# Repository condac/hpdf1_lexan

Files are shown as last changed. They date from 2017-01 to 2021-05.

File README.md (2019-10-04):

# HPD F1 Lexan version
Custom version of the HPD F1 to use lexan body. 

## About
This is my custom version of the HPD F1 by Kent Asplund. Ask questions and join discussion about these printed cars on Google+ https://plus.google.com/communities/117625327650679845498 You can also open an issue here on github if you have questions about the cars design or build process. 

## Material

All parts are designed to be printed in 100% infill. Use 2mm Perimiters and 0.15-0.2mm layer height as a start. Total material used is about 260g.

You can print every part in PLA and it will work suprisingly well. If you are printing this for the first time I recommend you print it in PLA or what ever your printer can handle best at first, and when something break you can print it in nylon.   

My race car have everything in PLA apart from some nylon changes I have made after some parts broke. There are 2 categories of nylon you want to use, a soft and flexible, and a hard. Where hard is still very soft compared to PLA. I have used Bridge nylon for flexible and 910 Alloy for harder. Here are my current changes and why:

* front_wing.stl & rear_wing.stl softer nylon for flex and impact resistance. (No rear wing in bridge nylon have been destroyed yet!!) 
* side_stab2.stl Soft or hard nylon for maximum impact resistance. I used Bridge here because it was in the printer at the time. 
* cradle_bottomPlate_wide.stl Soft or hard nylon for maximum impact resistance. This part takes alot of beating when the rear tires hit something. I used Bridge here because it was in the printer at the time and it worked well even if its soft.
* cradle_rightBulkhead.stl Hard nylon for high temperature. The motor get hot if you have a grippy surface like indoor carpets. Outdoor on normal asfalt or low grip racetracks there is no problem using PLA here. I have used nylon 910 and it flexes abit under the weight of the enginge but I have used it for a long time and it works. 

All parts can be made in nylon if you want maximum strength. The car is designed to not be to wobbly with the "hard" but still soft nylon material. I made all designs to be nylon printer friendly and the target design was to print everything in nylon. But after printing the prototype in PLA and crashing it I noticed that the new design was very good even with PLA so I have only changed a few parts to Nylon after they have breaked. 

## Non-printed parts
* Low-profile servo
* ESC + Motor
* Shorty LiPo-Pack
* 5pcs MR128-2RS Bearing
* 4pcs MR105-2RS Bearing
* 10pcs 3.175mm (1/8") Diff Balls
* 2pcs M14x28x1.5mm washer
* 170mm M4 threaded rod
* Carbon fiber rod OD 8mm ID 6mm 120mm (Note: All carbon fiber rods must be able to slide into each other)
* Carbon fiber rod OD 6mm ID 4mm 120mm
* Carbon fiber rod OD 10mm ID 8mm 120mm ( for future upgrade, still in development ) 
* 3pcs M3 Locknuts
* ~4pcs Mx6 button screws
* ~18pcs M3x10 button screws
* ~4pcs M3x12 button screws
* ~15pcs M3x16 button screws
* ~8pcs M3x10 Flat screws

## Bulding instructions

### Rear axle
The rear axle parts in this is for carbon fiber rods. 
M4 threaded rod 167mm
Carbon fiber rod OD 8mm ID 6mm 120mm
Carbon fiber rod OD 6mm ID 4mm 120mm

Alternative any other rods with same dimention or a 8mm rod with 4mm inner diameter. 

Cut carbon fiber rods to 120mm (longer is better than shorter, a longer axle can be compensated with washers, a shorter is useless)
You need 2 rods one 8mm outer diameter and one 6mm outer diameter both with 1mm thickness so you can slide the 6mm rod into the 8mm rod and then the M4 rod inside. And then glue them all together with the M4 sticking out 22mm on the right side (diff side). 

Place one regular M4 nut on the diff side with a washer between the nut and rods. The washer must be smaller than 8mm OD so bearings can slide over it. If you don't have washers that fit just ignore them. Don't tighthen the nut because this will break the glue inside. The nut is just there to take stress off the glue in case you crash or the glue fails. 

On the other side where we just want a wheel to fit place a <8mm washer if you have it and then 2 M4 Lock nuts placed with the nylon locking side towards each other. Do not tighten the nuts towards the rod to hard. Tighten the nuts against each other. These nuts will transfer all the torque from the axle to the wheel so tighten it hard against each other will make it stay in place. It will want to get loose on braking if your wheel nut is loose. Acceleration will make it self tightening so there is very little chance of it coming loose during driving. 

Last glue the indrive in place. Best way to place the indrive right is to screw on a extra m4 nut on the diff side and assemble everything with gears diffplates and diff balls and you will see where the indrive want to be placed. The extra M4 nut creates a perfect space inside, and when you remove it after gluing the indrive in place you will have a gap between the wheel and axle where it can rotate free. 

## Make stl

### In Linux (or OSX)
* checkout project
* Make sure you have OpenSCAD installed
* Type "make all" in prompt

### Manual in OpenSCAD (Windows users)
* open print.scad
* type the module name you want to print in the code and compile (F6)

## Working with the files
Having parts in different files and working with multiple OpenSCAD programs open for all files is working very good (for me atleast). When you save a file and change window to another file that have the other file as a previev or included part it will automaticly update it. And having git to save changes you want and don't want saving a lot when testing is not harmfull for your files even if you screw up because you can use git to revert to the last time you did a commit. 

print.scad is used to print parts in the right rotation for printing. 

hpdf1_lexan.scad is a preview to see all parts in the right places

## Donations
Feel free to make any donations on my patreon page https://www.patreon.com/condac or with paypal https://www.paypal.me/condac

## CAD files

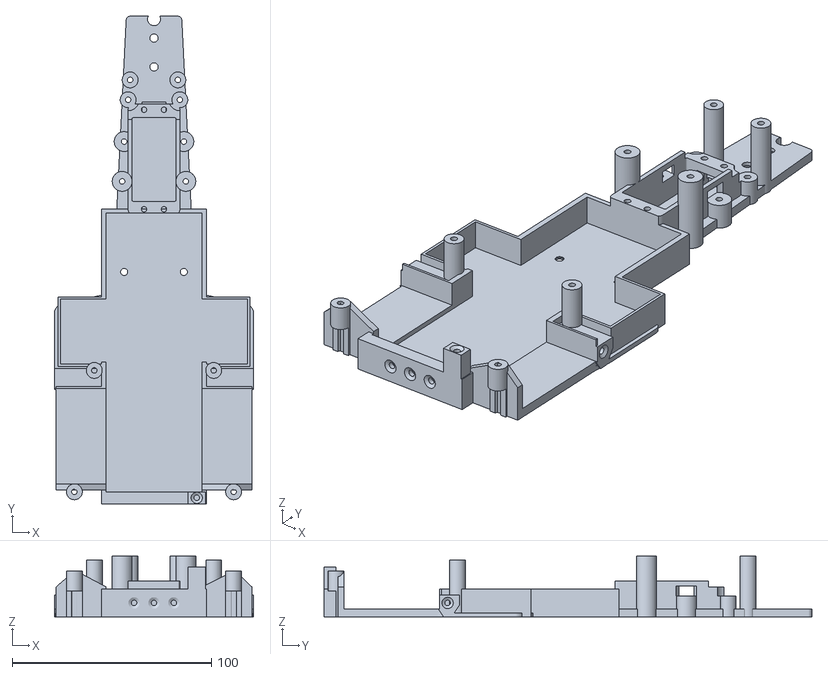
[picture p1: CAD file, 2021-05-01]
stl/biglipo_main_chassie.stl
100.0 x 245.0 x 30.5

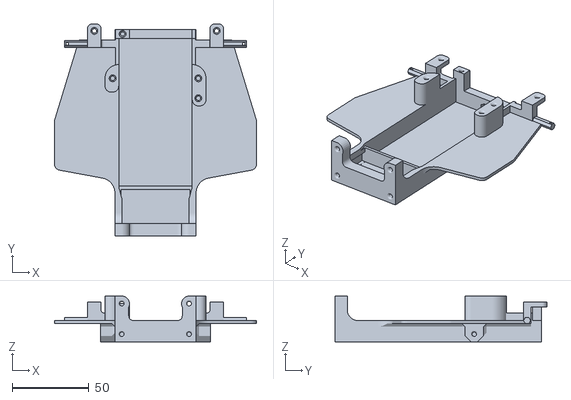
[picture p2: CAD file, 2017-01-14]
ref/main-chassis.stl
132.0 x 138.5 x 30.0

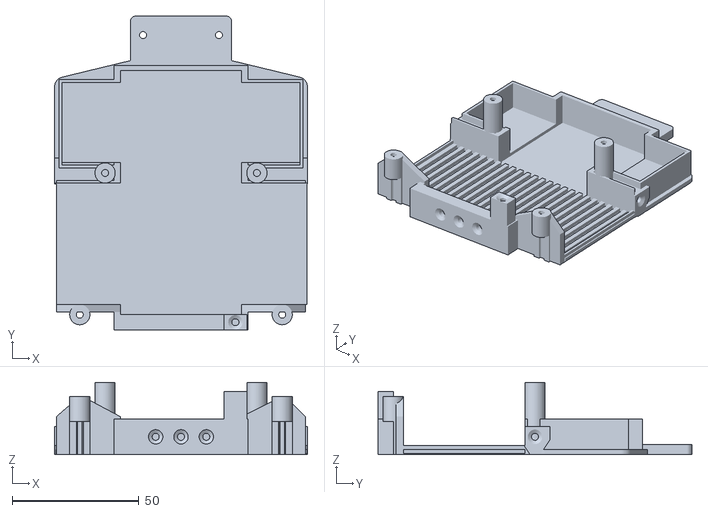
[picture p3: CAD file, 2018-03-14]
stl/main_chassie.stl
100.0 x 124.0 x 28.5

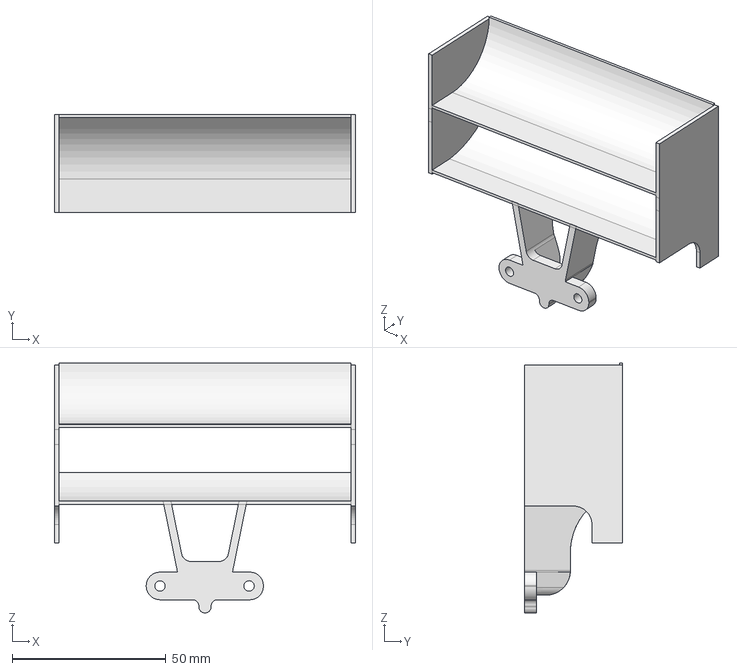
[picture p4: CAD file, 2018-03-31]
rear_wing.fcstd
98.0 x 32.0 x 81.4 mm

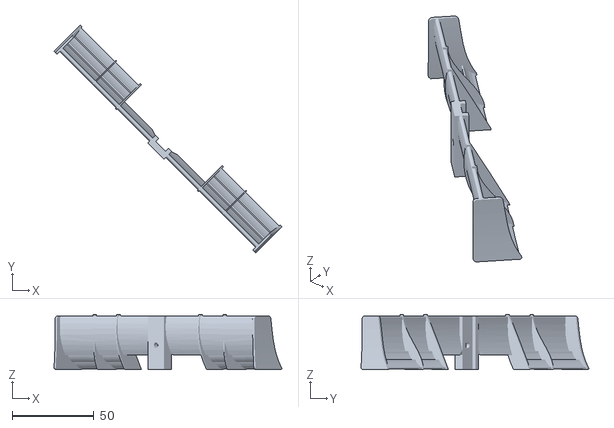
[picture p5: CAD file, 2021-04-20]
ref/Front-wing.stl
139.9 x 139.9 x 34.0

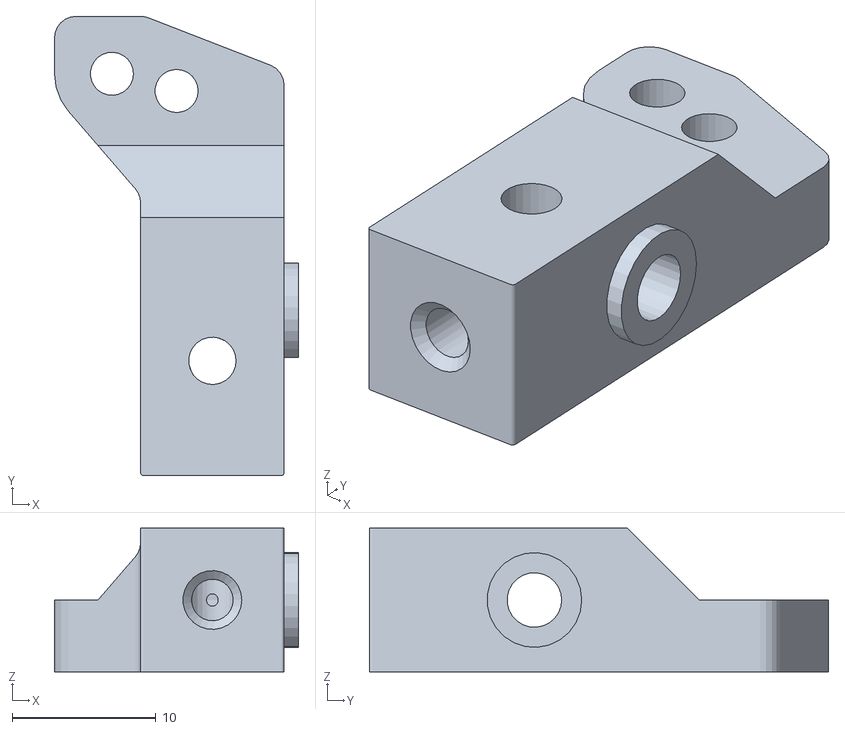
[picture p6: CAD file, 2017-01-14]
ref/testhub.stl
17.0 x 32.0 x 10.0

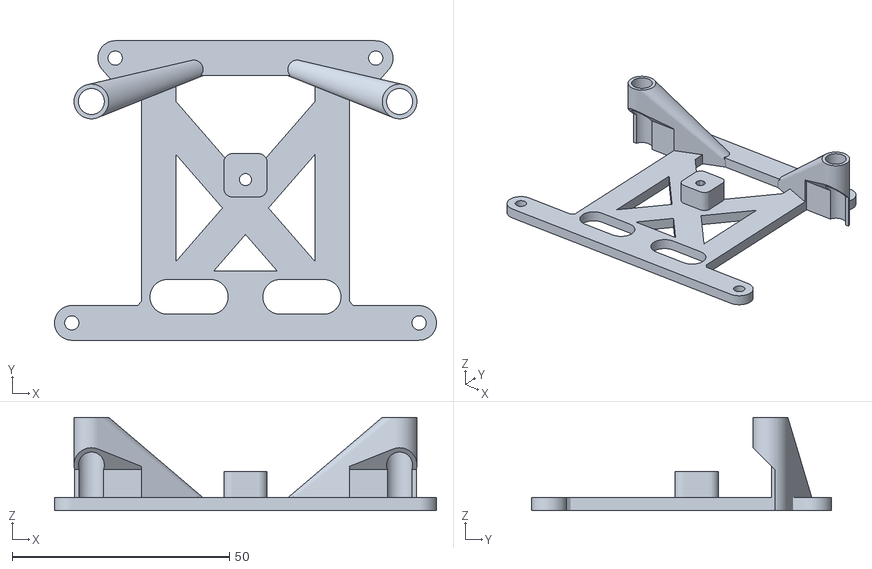
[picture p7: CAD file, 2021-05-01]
stl/biglipo_battery_plate.stl
88.0 x 69.0 x 21.5

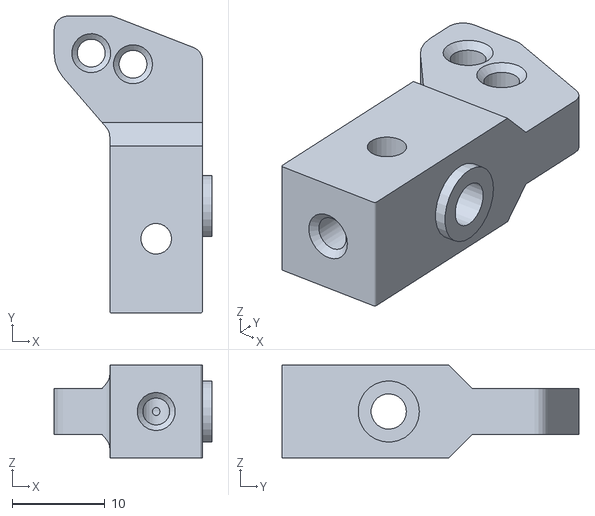
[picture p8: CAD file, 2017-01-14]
ref/steering-hub.stl
17.0 x 32.0 x 10.0

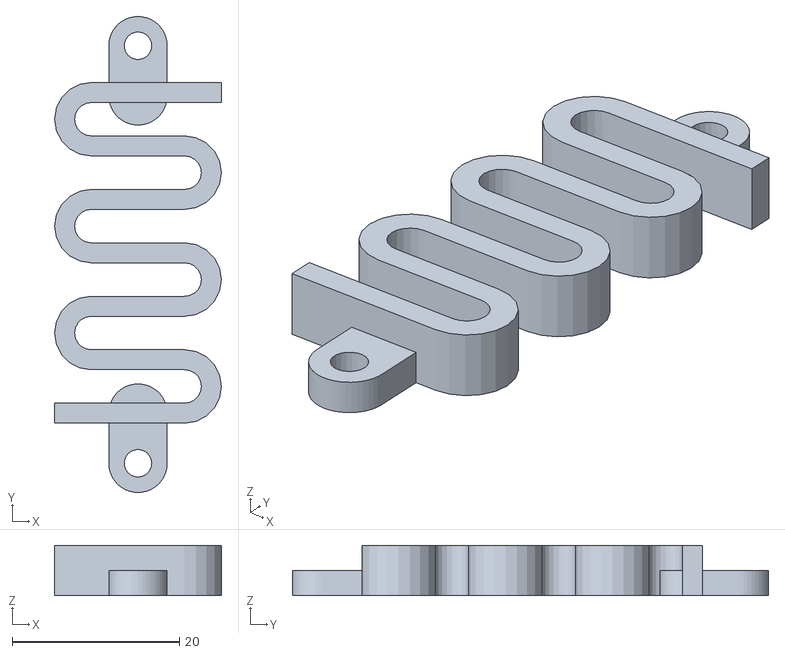
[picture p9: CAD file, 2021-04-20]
stl/plastic_rear_spring_6.stl
20.0 x 57.0 x 6.00

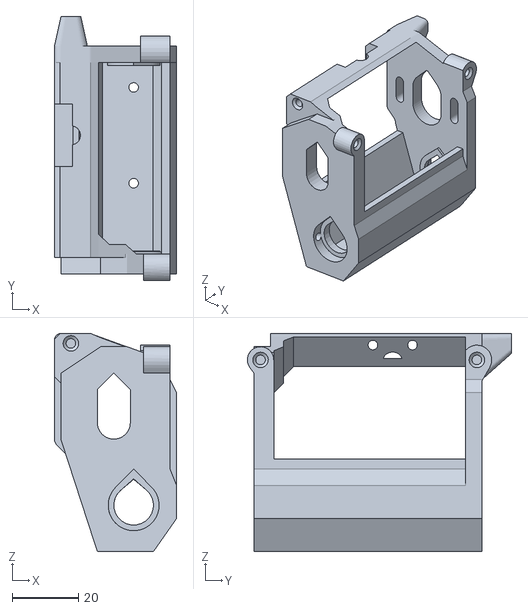
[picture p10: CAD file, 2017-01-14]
ref/Cradle.stl
37.0 x 80.0 x 66.0

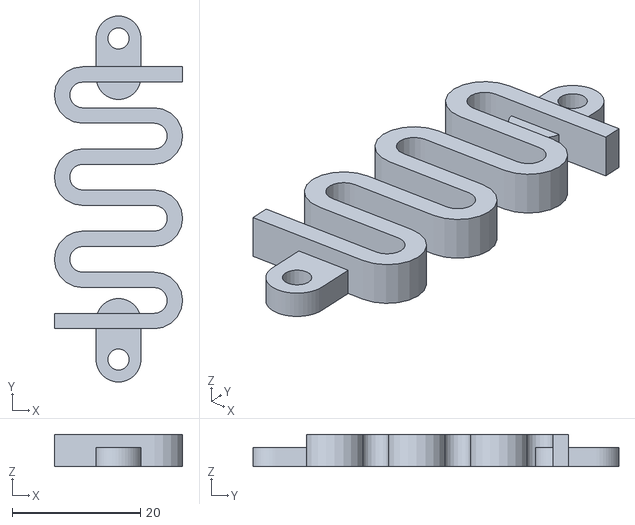
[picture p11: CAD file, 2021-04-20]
stl/plastic_rear_spring_5.stl
20.0 x 57.0 x 5.00

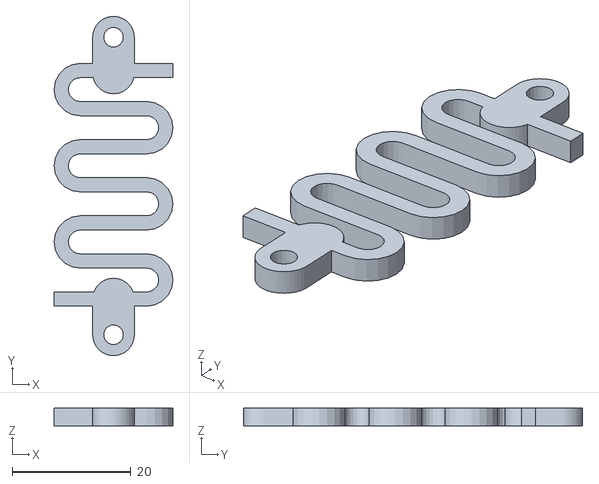
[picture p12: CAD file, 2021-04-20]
stl/plastic_rear_spring_3.stl
20.0 x 57.0 x 3.00

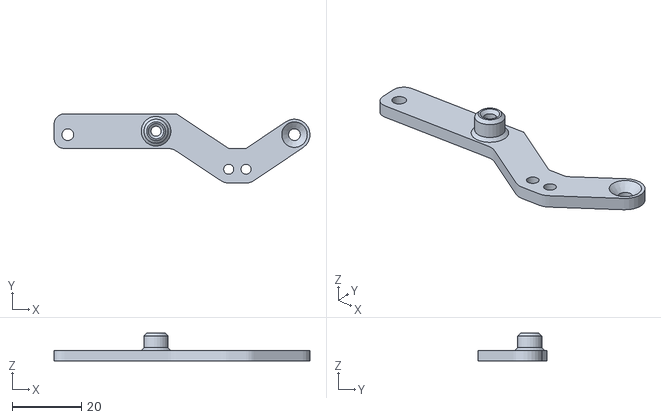
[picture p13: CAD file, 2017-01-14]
ref/rear-damper-mount.stl
74.0 x 20.0 x 8.00

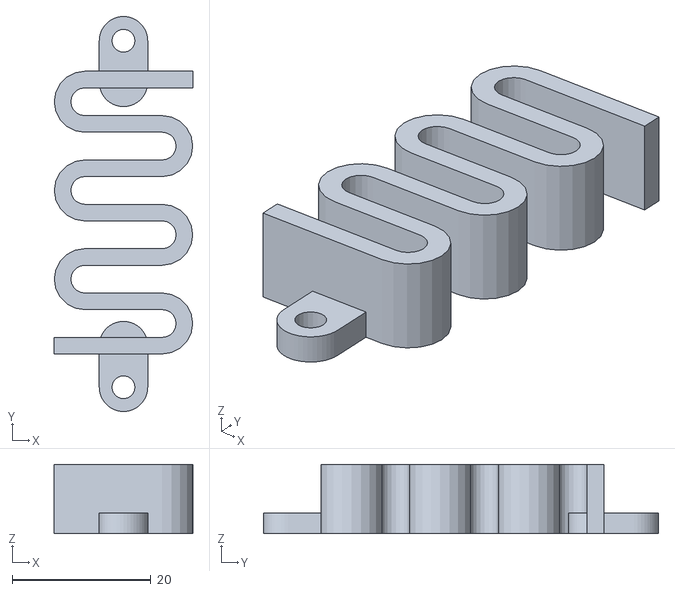
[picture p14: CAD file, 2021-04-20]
stl/plastic_rear_spring_10.stl
20.0 x 57.0 x 10.0

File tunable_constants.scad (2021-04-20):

// Change parameters to fit your printer and slicer differences

C_M3_DIAMETER = 3.3; // size of a hole that a M3 screw will slide through
C_M3_DIAMETER_THREAD = 2.8; // size of a hole that a M3 screw will create own threads in

C_M3_NUT = 7;

C_KINGPIN_LOOSE = 3.5; // The hole for kingpin in the arms that are suposed to slide
C_KINGPIN_SNUG = 3.3; // The hole in the steering hub where the kingpin is suposed to be tightly locked with a screw

C_M4_NUT = 8.4;

C_M4_DIAMETER = 4.1; // size of a hole that a M4 screw will slide through
C_M4_DIAMETER_THREAD = 3.8; // size of a hole that a M4 screw will create own threads in

    b_12mm_tol = 0.3; // tolerance for bearing with 12mm diameter

C_12MM_BEARING_D = 12+b_12mm_tol; // Size of a hole that hold a 12mm bearing
C_12MM_BEARING_H = 3.5;

C_8MM_LOOSE = 8.7; // Loose fitting that will guarantie that it will not touch
C_8MM_TIGHT = 8.2; // Tight fitting for indrive etc
C_8MM_FIT = 8.5; // Perfect fit for it to be removable but not by much force, used for left wheel mount

// ############# Settings ################
S_CASTER = 4;

S_CAMBER = 2;

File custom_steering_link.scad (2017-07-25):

// file for viewing parts when edit
include <tunable_constants.scad>;

use <lexan_main-chassie.scad>
use <lexan_nose.scad>
use <lexan_side_stab.scad>
use <caster_hub.scad>
use <wingadapter.scad>
use <common_parts.scad>

link_length = 51;
link_h = 3;
link_d = 5;

mount_d= 6;
mount_h = 3;
mount_hole = 3.3;

translate([0, -10, 36])steering_link_p();

module steering_link_p() {
    difference() {
        union() {
            hull() {
                translate([0, 0, 0])cylinder(d=link_d, h=link_h);
                translate([0, link_length, 0])  cylinder(d=link_d, h=link_h);
            }

            
            translate([0, 0, 0]) cylinder(d=mount_d, h=mount_h);
            translate([0, link_length, 0]) cylinder(d=mount_d, h=mount_h);
        }
        allScrews();
    }
}

%allScrews();
module allScrews() {

            translate([0, 0, 0]) cylinder(d=C_M3_DIAMETER, h=mount_h);
            translate([0, link_length, 0]) cylinder(d=C_M3_DIAMETER, h=mount_h);
}


module torus(dd=1, wall=1, hh=1) {
        difference() {
            cylinder(d=dd, h=hh);
            cylinder(d=dd-wall*2, h=hh);
        }
    
}

 %visualHelp();
module visualHelp() {


%translate([92.5, 80, 35.5])  rotate([0,0,180]) import("ref/RearDamperMountCarbon.stl", convexity=10);

color("green") side_spring_plate_p();

//nose_plate_p();
color("lightblue")main_chassie_p();

battery_plate_p();






}

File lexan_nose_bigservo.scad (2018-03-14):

use <lexan_main-chassie.scad>;
use <caster_hub.scad>;
use <common_parts.scad>
include <tunable_constants.scad>;
//basefornewnose
//%translate([28, -60, 0])  rotate([0,0,180]) import("basefornewnose.stl", convexity=10);

// main-chassie
//translate([-62,240-25,23]) %caster_p();
%main_chassie_p();
%nose_plate_p();
//%translate([28, -65, 0])  rotate([0,0,180]) import("main.stl", convexity=10);
//translate([28+28+28+15, -20, -91])  rotate([-90,0,0]) rotate([0,0,180]) %import("body.stl", convexity=10);

long = true;
long_extra = 0; // set to 0 if short 42 if long battery
long_extra2 = 0; // set to 0 if short 18 if long battery
//long = false;

//batteri
batteri_x = 48;
batteri_y = 96.5+long_extra;
batteri_z = 28;
b_offset_z = 2; // höjden batteriet ligger på, det som blir basens tjocklek i botten


servo_hojd = 20.5; // höjden på servot upp och ner till fästet

translate()cube(2);
translate([0,240-100,28]) rotate([-90,180,0]) bigservo();
module bigservo() {
    translate([0,9,49]) rotate([0,180,0]) rotate([0,0,90]) rotate([90,0,0]) import("ref/servoarm.stl", convexity=10);
    translate([-10,-55/2,30-3.5]) cube([20,55,3.5]);
    translate([-10,-41/2,0]) cube([20,41,38]);
}

if (long) {
    echo("long");
    batteri_y = 96.5+long_extra;
} else {
    echo("short");
    batteri_y = 96.5; // 138mm för lång ack
}

// bas
b_x = 53;
b_y = 135+long_extra2;
b_z = 14;

bakre_wall = 6;

//plattan
p_x = 132/2; // bredden på plattan delat med 2
p_b_x = 100/2; // bredden på plattan bak
p_y = 92;
p_z = 2;
p_offset_z = b_z-p_z;
p_bak_offset = 7;

// Fjädrar

s_x = 80/2;
s_z = 12;
s_wall = 5; // väggtjocklek
s_wall_x = 9; // väggbredd
s_plate_z = 3; // plattans tjocklek
s_plate_y = 11; // hur långt bak plattan sticker ut
s_plate_h_y = 6.1; // hur långt bak hålet ska va

// skruvar
//$fs= 0.4;
m3_d = C_M3_DIAMETER;//3; // hål som en skruv inte ska fästa i
m3_d_s = C_M3_DIAMETER_THREAD; // 2.8; // hål som skruven ska skapa gängor i

// front mount
fm_y = 8;
fm_z = 30;
fm_screw_dist_z = 20;
fm_screw_dist_x = 44;

// lilla badkaret
lb_wall = 2; // väggen mellan lilla och batteriet
lb_x = batteri_x;
lb_y = b_y-lb_wall-bakre_wall-fm_y-batteri_y;
lb_z = batteri_z;

// sidofästen
sf_y = 44;

//####################################################

%nose_p();
translate([0,240,0]) lower_arm();

translate([0,240,0]) arm_plate();

translate([0,240,0]) upper_arm();

translate([0,115,30]) upper_arm_plate_p();

// ###################################################
color("yellow") %mirror([1,0,0]) translate([0,240,0]) upper_arm();
color("yellow") %mirror([1,0,0]) translate([0,240,0]) lower_arm();


// visual aids
color("yellow") % translate([-15,240-10-25, 56.5]) cube([30, 10, 1]);
color("yellow") % translate([-15,240-10-75, 42]) cube([30, 10, 1]);

// servoräddaren/arm
translate([0,240-42-5-13.5,34]) %cylinder(r=23, h = 3);
translate([0,240-42-5-13.5,34-3]) %cylinder(r=5, h = 3);
//main_chassie();

n_y = 115;
n_x1 = 28; // x fram
n_x2 = 37; // x bak
n_z = 4;

// vingfästen
wf_y = 11;
wf_dist = 14.5;

module nose_p() {
    
    translate([0,240-n_y,0]) difference() {
        union() {
            //%translate([-n_x1/2,0,0]) cube([n_x1, n_y, n_z]);
            hull() {
                translate([n_x1/2-2,n_y-2,0 ]) cylinder(d=4, h=n_z);
                translate([-n_x1/2+2,n_y-2,0 ]) cylinder(d=4, h=n_z);
                translate([n_x2/2-2,2,0 ]) cylinder(d=4, h=n_z);
                translate([-n_x2/2+2,2,0 ]) cylinder(d=4, h=n_z);
            }
            //translate([0,8,0]) front_mount(); // fästet mot main_chassie
            //translate([0,8,0]) mirror([1,0,0]) front_mount(); // fästet mot main_chassie
            //translate([-n_x2/2,0,0])  cube([n_x2, 8, 14]); // mount mitten block
            
            // Servomount
            translate([0,n_y-105+6+27,0]) servo_mount();
            
            // bärarmar mount
            lower_arm_mount();
            mirror([1,0,0]) lower_arm_mount();
            upper_arm_mount();
            mirror([1,0,0]) upper_arm_mount();
            
        }
        
        // skruvar fäste main chassie
        translate([ 15, 8, 0]) rotate([0,0,0]) common_flat_screw_tap();
        translate([-15, 8, 0]) rotate([0,0,0]) common_flat_screw_tap();
        
        //utsågning för skruvar i framfäste
        translate([ 15, 8, 0]) cylinder(d=m3_d, h= 5);
        translate([-15, 8, 0]) cylinder(d=m3_d, h= 5);
        
        // Utsågning för bararmar fram 
        translate([0,n_y,0]) lower_arm_mount_cut(dd=m3_d_s);
        translate([0,n_y,0]) mirror([1,0,0])  lower_arm_mount_cut(dd=m3_d_s);
        translate([0,n_y,0]) upper_arm_mount_cut(dd=m3_d_s);
        translate([0,n_y,0]) mirror([1,0,0])  upper_arm_mount_cut(dd=m3_d_s);
        //translate([0,n_y,0]) translate([-15, -53, 10.5]) cylinder(d=7, h=3.5+0.5);
        //translate([0,n_y,0]) mirror([1,0,0]) translate([-15, -53, 10.5]) cylinder(d=7, h=3.5+0.5);
        
        // servo badkkar
        translate([0,6+27,0]) translate([-24/2+1, n_y-105-42/2, 1]) roundedcube(22, 42, 18, 0.5);
        // servokabel
        translate([0,6+27+8,0]) translate([-12/2,n_y-105 -42/2, 1]) cube([12, 42, 10]);
        // servot är ivägen för lower arm plate
        translate([la1_x,n_y-la1_y,n_z+11-3.5-1 ]) cylinder(d=11, h=n_z+11-3.5-1);
        translate([-la1_x,n_y-la1_y,n_z+11-3.5-1 ]) cylinder(d=11, h=n_z+11-3.5-1);
        
        // vingfästen
        translate([0,n_y-wf_y,-1]) cylinder(d=4.2, h= n_z*2);
        translate([0,n_y-wf_y-wf_dist,-1]) cylinder(d=4.2, h= n_z*2);
        
        translate([0,n_y-wf_y,-1]) cylinder(d1=11, d2=4.2,  h=3.5);
        translate([0,n_y-wf_y-wf_dist,-1]) cylinder(d1=11, d2=4.2, h= 3.5);
        
        //hål för att kunna skruva bodypost i vingfästet
        translate([0,n_y-1.5,0]) cylinder(d=6.5, h=n_z);
        
    }
}

module arm_plate() {
    difference() {
        union() {
            translate([-20/2,-45-5,15]) cube([20, 45, 3]);
            translate([-la1_x, -la1_y, 14]) cylinder(d=10, h=4);
            mirror([1,0,0]) translate([-la1_x, -la1_y, 14]) cylinder(d=10, h=4);
        }
        translate([-la1_x, -la1_y, 13]) cylinder(d=m3_d, h=5);
        mirror([1,0,0]) translate([-la1_x, -la1_y, 13]) cylinder(d=m3_d, h=5);
        // vingfästen
        translate([0,-wf_y,-1])  cylinder(d=3.8, h= 50);
        translate([0,-wf_y-wf_dist,-1]) cylinder(d=3.8, h= 50);
        //karosspinnen
        translate([0,-wf_y+9,-1]) cylinder(d=10, h= 50);
        
        // servosrkuvar
        translate([5, -42-5,15])  cylinder(d=m3_d, h=3);
        translate([-5, -42-5,15])  cylinder(d=m3_d, h=s_z);
        
        // upperarmmountspost
        translate([-ua1_x, -ua1_y, 14]) cylinder(d=10, h=4);
        mirror([1,0,0]) translate([-ua1_x, -ua1_y, 14]) cylinder(d=10, h=4);
    }
}

module upper_arm_plate_p() {
    
    difference() {
        hull() {
            translate([-ua1_x,n_y-ua1_y,0 ]) cylinder(d=8, h=2.5);
            translate([ua1_x,n_y-ua1_y,0 ]) cylinder(d=8, h=2.5);
        }
        translate([-ua1_x,n_y-ua1_y,0 ]) cylinder(d=m3_d, h=2.5);
        translate([ua1_x,n_y-ua1_y,0 ]) cylinder(d=m3_d, h=2.5);
        
    }
    
}

la1_x = 13;
la1_y = 42;
la2_x = 15;
la2_y = 63;

ua1_x = 12;
ua1_y = 32;
ua2_x = 16;
ua2_y = 83;


module arm_pin_p() {
    difference() {
        translate([-52, -25, 14]) cylinder(d=m3_d_s+0.8*4, h=36.5-14-4);
        translate([-52, -25, 14]) cylinder(d=m3_d_s, h=36.5-14-4);
    }
}
module lower_arm() {
    z_w = 3.5;
    z_z = 14;
    
    difference() {
        union() {
            hull() {
                translate([-la1_x, -la1_y, z_z-z_w]) cylinder(d=10, h=z_w);
                translate([-62, -25, z_z-z_w]) cylinder(d=10, h=z_w);
            }
            hull() {
                translate([-la2_x, -la2_y, z_z-z_w]) cylinder(d=6, h=z_w);
                translate([-52, -25, z_z-z_w]) cylinder(d=10, h=z_w);
            }
        }
        lower_arm_mount_cut(dd=m3_d);
        //translate([-62, -25, z_z-z_w]) cylinder(d=3.3, h=z_w);
        translate([-63, -23, 0]) caster_rod();
        translate([-52, -25, z_z-z_w]) cylinder(d=m3_d, h=z_w);
        %arm_pin_p();
    }
}
module lower_arm_mount() {
    translate([-la1_x,n_y-la1_y,0 ]) cylinder(d=8, h=n_z+11-3.5-1);
    translate([-la2_x,n_y-la2_y,0 ]) cylinder(d=10, h=n_z+11-3.5-1);
}
module lower_arm_mount_cut(dd=3) {
    z_w = 3.5;
    z_z = 14;
    translate([-la1_x, -la1_y, z_z-z_w]) cylinder(d=dd, h=z_w);
    translate([-la2_x, -la2_y, z_z-z_w]) cylinder(d=dd, h=z_w);
    //translate([-62, -25, z_z-z_w]) cylinder(d=dd, h=z_w);
    translate([-la1_x, -la1_y, 0])  common_flat_screw_tap(l=11.1);
    translate([-la2_x, -la2_y, 0]) common_flat_screw_tap(l=11.1);
    
    
}
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

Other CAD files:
stl/plastic_rear_spring_4.stl
stl/plastic_rear_spring_9.stl
stl/plastic_rear_spring_8.stl
stl/plastic_rear_spring_7.stl
lexan_steering_hub.scad
biglipo_main-chassie.scad
biglipo_nose.scad
bodyposts.scad
caster_hub.scad
common_parts.scad
custom_spring.scad
diffuser.scad
front_body.scad
frontwing.scad
hpdf1_Lexan.scad
hpdf1_Lexan_BigLipo.scad
hpdf1_printedbody.scad
hpdf1_rear_cradle_universal.scad
legacy parts to keep/bearing_adapter8mm_tjockare.stl
legacy parts to keep/cradle_bottomPlate.stl
legacy parts to keep/cradle_leftBulkhead.stl
legacy parts to keep/cradle_rightBulkhead.stl
legacy parts to keep/lower_arms_innan storre.stl
legacy parts to keep/nose_plate.stl
lexan_H_plate.scad
lexan_main-chassie.scad
lexan_nose.scad
lexan_nose_legacy.scad
lexan_side_stab.scad
print.scad
rear_axle.scad
ref/spring.scad
servo_arm.scad
side_damper.scad
spacers.scad
stl/arm_pin.stl
stl/battery_plate.stl
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

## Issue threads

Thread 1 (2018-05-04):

Create 3dprinted rear axle

condac, 2018-05-04:
Try to make a 3d printed rear axle that prints flat on the printbed. Use a 3mm threaded rod through the whole thing or just in the ends.

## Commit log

2017-01-14 removed unwanted file
    [all.stl]
2017-01-25 new files
    [battery_plate.stl, bodyposts.scad, caster_hub.scad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]
2017-01-27 Lots of fixes before first test drive
    [bodyposts.scad, caster_hub.scad, hpdf1_Lexan.scad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]
2017-01-31 fixes after testdrive
    [caster_hub.scad, lexan_main-chassie.scad, print.scad]
2017-01-31 updated stls
    [battery_plate.stl, body_posts.stl, lower_arm_plate.stl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]
2017-03-12 bugfixes after testing
    [battery_plate.stl, body_posts.stl, hpdf1_Lexan.scad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]
2017-05-24 wider mount for rear cradle
    [arm_pin.stl, battery_plate.stl, body_posts.stl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]
2017-05-24 New rear cradle and frontwing
    [battery_plate.stl, body_posts.stl, common_parts.scad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]
2017-06-02 Rear axle parts
    [frontwing.scad, hpdf1_Lexan.scad, hpdf1_rear_cradle_universal.scad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]
2017-06-04 pars for rear axle completed
    [hpdf1_Lexan.scad, hpdf1_rear_cradle_universal.scad, indrive.stl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]
2017-06-10 plastic spring, lots of small fix
    [arm_pin.stl, battery_plate.stl, body_posts.stl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]
2017-07-25 Lots of small changes
    [battery_plate.stl, body_posts.stl, bodyposts.scad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]
2017-07-25 New nose for bigger lower arm mounting
    [lexan_nose.scad, lexan_nose_bigservo.scad, nose.stl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]
2017-07-28 side damper, front wing, printed gears
    [arm_pin.stl, battery_plate.stl, body_posts.stl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]
2017-09-29 random changes
    [custom_spring.scad, lexan_main-chassie.scad, lexan_nose_bigservo.scad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]
2017-09-29 stronger sidestab
    [lexan_side_stab.scad]
2017-09-29 new pinions etc...
    [cradle_bottomPlate_wide.stl, front_body.scad, hpdf1_printedbody.scad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]
2017-09-30 stronger sidestabs
    [lexan_side_stab.scad]
2017-10-09 lite tjockare indrive
    [rear_axle.scad]
2018-03-14 Lots of changes at once, sorry for the mess...
    [bearing_adapter8mm_tjockare.stl, bengts vinge.stl, cradle_bottomPlate.stl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]
2018-03-14 updated stl files
    [arm_pin.stl, battery_plate.stl, body_posts.stl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]
2018-03-25 Arm pin moved to 50mm, Indicators for caster and camber
    [caster_hub.scad, common_parts.scad, lexan_nose.scad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]
2018-03-31 rear wing
    [cradle_bottomPlate.stl, cradle_bottomPlate_wide.stl, cradle_damperMount.stl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]
2018-05-14 new servo arm
    [servo_arm.scad]
2018-05-18 arms follow caster with hole
    [lexan_nose.scad, lexan_side_stab.scad]
2021-04-20 unsycronised changes
    [arm_pin.stl, battery_plate.stl, body_posts.stl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]
2021-04-20 used reference files
    [Front-wing.stl, spring.scad]
2021-04-30 small fixes
    [common_parts.scad, custom_spring.scad, hpdf1_Lexan.scad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]
2021-04-30 bigLiPo prototype
    [biglipo_main-chassie.scad, biglipo_nose.scad, hpdf1_Lexan_BigLipo.scad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]
2021-05-01 bigLipo first prototype stl
    [biglipo_battery_plate.stl, biglipo_main_chassie.stl]
